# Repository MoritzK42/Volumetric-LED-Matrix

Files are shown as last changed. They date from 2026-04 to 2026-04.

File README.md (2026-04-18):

# Volumetric LED Matrix
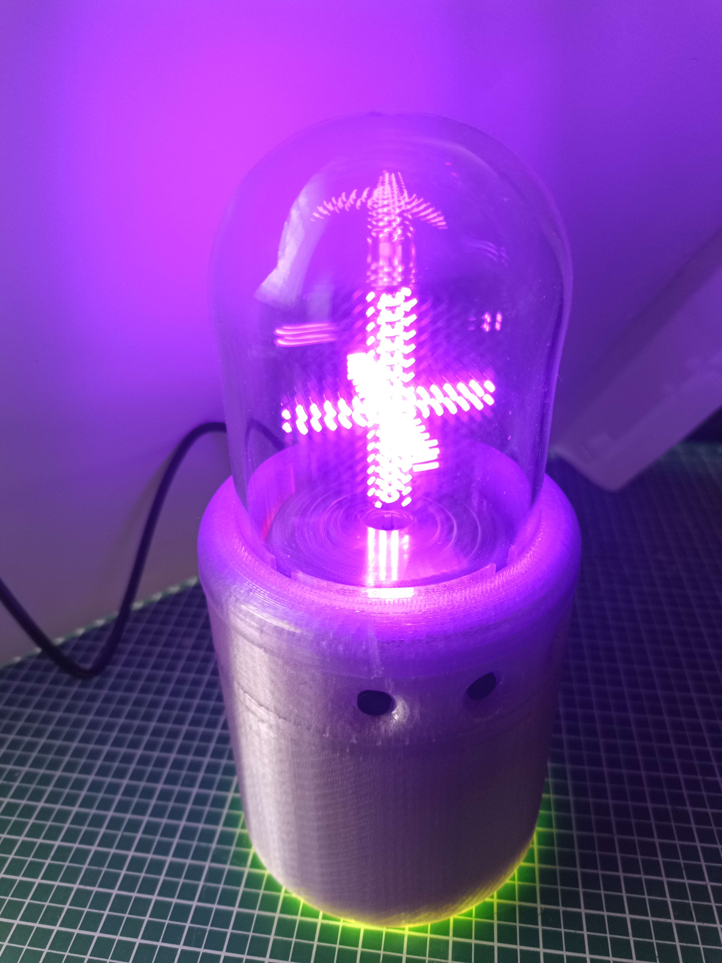
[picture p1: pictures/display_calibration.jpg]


## About the project
This project was inspired by mitxelas tiny volumetric LED display and Nick electronics volumetric lamp project.
It was created in the context of the elective project of the Hochschule für angewandte Wissenschaften (HAW) Hamburg, Germany.
The matrix can display 3D animations on a spinning 16x16 LED matrix, and is powered via USB-C. 

## Hardware
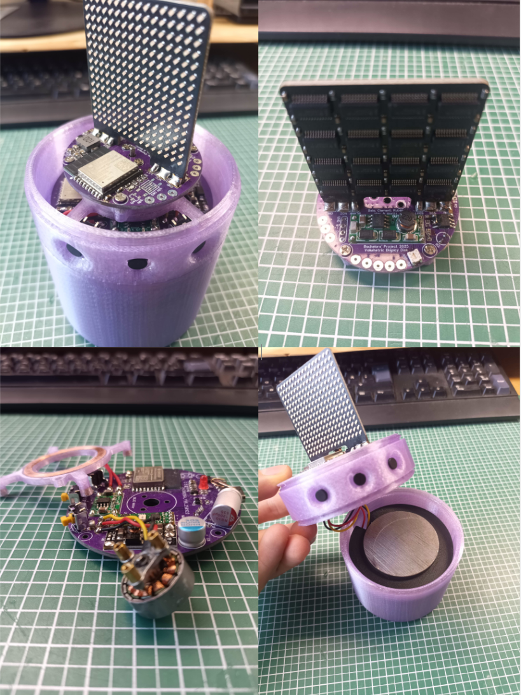
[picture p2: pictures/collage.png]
more pictures can be found in the pictures folder

All used machine screws used are M2 with philips head bought on AliExpress. The used lengths are the following:

For disc to motor: 4 mm

For upper coil holder to PCB: 5 mm

For motor and lower coil holder: 8 mm

The motor stands on 4 mm standoffs, which are spaced with M2 washers to not pierce the motor coils.

All screws must be assembled with loctite for reliable long term use.

The used wireless module is 5V / 1A from AliExpress: https://de.aliexpress.com/item/1005006105734663.html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

The LED RGB ring is 16 LEDs WS2812 RGB module from AliExpress: https://www.aliexpress.com/item/1005006579026411.html?spm=a2g0o.order_list.order_list_main.15.7f645c5fj35ANH

The glass dome was bought on AliExpress

The 12 V mini step up module was bought on AliExpress: https://de.aliexpress.com/item/1005005835656823.html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

The ESC module was bought an AliExpress: https://de.aliexpress.com/item/1005008034100991.html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 (8 A Version)

The BLDC motor was bought on AliExpress: https://de.aliexpress.com/item/1005006110056005.html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

The 16x16 LED Matrix was assembled by JLCPCB PCBA service.

The other circuit boards where assembled by hand.

The wireless coils where glued into the holders (make sure to remove the small piece of tape beforehand) with superglue.
Unfortunately, the matrix suffers from imbalance and thus heavy vibrations when spun. Thus, a 50 mm diameter and 52 mm tall piece of round steel was integrated into to the base as counterweight, aswell as a silicone pad on the bottom to further dampen vibrations. The power to the spinning top part is transported wireless from the base.
The choosen BLDC ESC was rather cheap and especially with a weak power supply, the motor cannot be started up.
The 5 V USB-C power supply must be strong. Not all power supplys work. Anker power banks and supplys have tested good for purpose of powering the volumetric led matrix.
Sometimes the animations or pictures show small glitches. This is a known issue still to be solved.
The filament for the wireless coil spool holders must be capable to withstand higher temperatures without bending itself.
Also, a 1200 uF polymer capacitor was added between USB-C 5 V and GND to further improve stability. Two 22 uf 0805 ceramic capacitors have been added to the base ESP32 input in parallel to the 100 nf and 10 uf decoupling capacitors since there have been issues with the ESP32 crashing when sending wireless commands to the disc ESP32. This issue may have been fixed also by reducing the TX power level in software.

## Software and operation
The Bitmap converter is written in C# and used to convert the Blender generated bitmaps of a frame or animation into a single header file containing a 4-dimensional array. 

The dimensions of the array have the following function:
```c
const uint8_t calibration[8][1][96][32] =
```

1. brightness compensation
2. frame of animation (1 for single 3D Image)
3. subframe (we decided to use 96 subframes per rotation in this project)
4. The single bytes making up the 256 bit LED matrix (8 x 32 = 256)

### Brightness compensation
Since the LEDs closer to the center of the cylindrical axis og the matrix have a lower distance to travel than the outer ones, they would appear to be brighter and thus overexpose the image. To mitigate this, the Bitmap converter automatically compensates the brightness and makes 8 additional frames which are compensated. This is at expense of MCU Flash, because now all frames take up eight times as much flash. But reducing the brightness in run by the MCU has proven to be too slow and would thus hinder a smooth display of the individual frames.

### Led Matrix Base
The LED matrix base containing the motor, buttons, wireless transmitter, 12 V step-up module, the RGB LED ring and position LED is controlled via an ESP32-C3. After plugging in the power, the ESP32 will flash the debugging LED twice and then fade the RGB ring through the colors. After pressing the left button, it will switch on the power to the wireless coil and ESC, which will in turn beep 3 times and turn on if initialized successful. The ESP32 on the disc will be powered and send an acknowledgement if it detects spinning. If not, the ESC initialisation has failed and the base ESP32 will power cycle the ESC to try again. Unfortunately this was the only way the reliably turn on the ESC, since 5 V USB-C supply seemed to be a poor choice and the ESC in general of poor quality. After successful turn on of motor and display, the animations can be cycled trough by pressing the center and right button. A long press will slowly spin the 3D object or animation. When the left button is pressed again, the motor stops and a 2D animation is displayed. The power to ESC and wireless transmitter is cut after 1 min in this state, to mitigate the issue of overheating coils and bent filament if left forgotten in this state.

### Led Matrix Disc
The LED matrix disc containing the LED matrix and LDR with comparator is also controlled via an ESP32-C3. The ESP32 references the start of a rotation via the comparator which compares the voltage from an LDR-resistor divider and potentiometer. Then the time of a rotation is sliced into 96 pieces where the subframes are displayed, altough, the timing is even more precise since there is also the aforementioned brightness compensation and also a settable percentage of on-time 96th time slot the create an effect of single LED dots. Thus, the code is highly optimized to deal with these very strict timing limitations and the hardware SPI-Bus is used to shift out the bits to the display drivers as fast as possible. The LEDs are not multiplexed, since this would, at these already super high refresh rates be almost impossible to deal with. Instead the TI 
The LED matrix disc containing the LED matrix and LDR with comparator is also controlled via an ESP32-C3. The ESP32 references the start of a rotation via the comparator which compares the voltage from an LDR-resistor divider and potentiometer. Then the time of a rotation is sliced into 96 pieces where the subframes are displayed, altough, the timing is even more precise since there is also the aforementioned brightness compensation and also a settable percentage of on-time 96th time slot the create an effect of single LED dots. Thus, the code is highly optimized to deal with these very strict timing limitations and the hardware SPI-Bus is used to shift out the bits to the display drivers as fast as possible. The LEDs are not multiplexed, since this would, at these already super high refresh rates be almost impossible to deal. Instead the 16 bit TI TLC59283DBQR serial shift register LED drivers ICs have been used to drive the LEDs. This choice has proven to be very effective, since the LED Matrix PCBA has performed absolutely flawlessly.

## Rendering animations in Blender
The 3D-Objects can be created in blender. They are then sliced and photographed in 1/96 increments of rotation. To create animations, the process must be repeated with all frames. The naming sceme which can be set in Blender when exporting has to be the following: "nameXX_YY", whereas the XX indicates the number of frame in the animation, and YY indicates the number of subframe in frame. A leading 0 must be added for numbers below 10. A python script in was written in Blender, to automate this process. Powerful hardware must be used to render the frames. They must be exported as singular bitmaps and then they must converted into suitable arrays by the bitmap converter tool. The converted arrays must then be included as header files to the volumetric led matrix disc code.

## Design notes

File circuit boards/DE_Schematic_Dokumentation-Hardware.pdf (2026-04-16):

A | A
B | B
C | C
D | D
E | E
F | F

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
TITLE:
Volumetric Display Assembly Dokumentation | REV: 1.0
Date: | 2025-10-01

Sheet: 1/1
Drawn By: MoritzK

Company: -

## LED Matrix - Reihenfolge Treiber

1 | 2 | 3

4

8

5 | 6 | 7

12

9 | 10 | 11
13 | 14 | 15

Die LED Matrix umfasst eine Gesamtanzahl von 16 x 16 = 256 LEDs.
Die LEDs werden mithilfe von dem LED-Treiber Baustein TLC59283 angesteuert.
Ein LED Treiber kann 16 LEDs ansteuern, weswegen 16 LED Treiber pro Matrix verbaut sind. Um die Leiterbahnenwege m glichst kurz zu halten,
steuern ein Treiber jeweils eine Submatrix von 4 x 4 = 16 LEDs an.

Die Zahlen in der oben stehenden Zeichnung verdeutlichen die Reihenfolge der LED Treiber.

Die LED Treiber werden Seriell ber den SPI-Bus angesteuert.
Ein LED wird mit 16 Bit = 2 Byte Daten gef llt. Sie arbeiten nach dem Shift-Register Prinzip, dass hei t, wenn ein neues Bit an Position 0 gespeichert wird,
r ckt Bit 0 an die Stelle von Bit 1, Bit 1 an die Stelle von Bit 2 usw.
Das letzte Bit, Bit 15 wird dann ber den Serial-Out des vorherigen LED Treibers
zum n chsten LED Treiber Serial-In weitergereicht.
Somit kann die ganze LED Matrix als ein gro er, 256 Bit umfassender Shift-Register betrachtet werden.

## LED Matrix - Submatrix

0 | 1 | 2 | 3
4 | 5 | 6 | 7
11 10 | 9 | 8

15 14 13 12

0

Die entprechende LUT ist als Textdatei in dem Dokumentationsordner enthalten

Die LEDs in der Submatrix mussten leider aus Platz- und Kostengr nden in einer solchen aus Softwaresicht "komischen" Reihenfolge angeordnet werden.

(0,0)

X

Y

(16,16)

(16,0)

(0,16)

So mit m ssen die Koordinaten mithilfe einer Look-Up-Tabelle (LUT)
in die Bit-Position des 256-Bit langen Frames umgewandelt werden.
Die 2D Position (0,0) w rde dann der Bit-Position 12 * 16 + 4 = 196 im 1D Frame entsprechen.
LED Matrix | Disc

# Dokumentation Hardware Volumetric LED Matrix

Der Strom durch die LEDs wird durch einen Widerstand am IREF-Pin der jeweiligen LED-Treiber eingestellt. Der Widerstand wurde auf 15 kOhm festgelegt, was einem Strom pro LED von
(1,208 V / 15 kOhm) * 43,8 = 3,53 mA entspricht.
Der LED Treiber braucht je nach Zustand bis zu max. 11 mA.
Somit betr gt die Maximale Leistungsaufnahme: 3,3 V * 16 * (3,53 mA * 16 + 11 mA) = 3,56 W Die LED Treiber sind nicht dimmbar, jedoch kann bei ausreichend hoher Aktualisierungsrate eine Totzeit implementiert werden, welche einen Dimm-Effekt verursachen kann.
Die Maximale SPI-Frequenz des LED Treibers betr gt 35 MHz.

IO6 - SDAT Serial Data
IO4 - SCLK Serial Clock
IO7 - LAT

Die Ausg nge der LED Treiber werden entsprechend des Zustandes des
internen Shift-Registers angesteuert.

LAT

(Kurzzeitig nach bertragung des Bit-Frames high setzen, um LEDs zu aktualisieren.)

IO3 - BLANK

BLANK
Alle Ausg nge werden abgeschaltet.

IO0 - PULSE

PULSE
Ein Signal pro Umdrehung

IO1 - LED

LED
On-board LED zu Debuggingzwecken

## Pinbelegung ESP32

## Verwendeter Microcontroller:

ESP32-C3-WROOM-02-N4

Die Aktuelle Umdrehungsfrequenz wird mit einem LDR (Light Dependent Resistor) gemessen. Dazu befindet sich auf der Base eine durchgehend leuchtende LED, welche auf die Disc scheint.

LED

LDR

Disc

Base
Der LDR erzeugt ber einen Spannungsteiler
eine Sinusf rmiges Signal, welches mithilfe eines Komparators in rechteckf rmiges Signal umgewandelt wird.

verarbeitet werden.

Somit kann es einfach digital vom ESP32

Die Triggerschwelle kann im ersten Prototyp durch Pot R6
eingestellt werden.
Nach erfolgreicher Einstellung kann in den n chsten Modellen ein fester Widerstand verbaut werden.

## Umdrehungssignal

## VCC Supervisor

Falls Probleme durch instabile Stromversorgung auftreten, kann optional
ein VCC Supervisor IC verbaut werden, welcher den ESP32 bei einer Spannung von kleiner 2,93 V zur cksetzt.

# Base

## Pinbelegung ESP32

IO6 - BTN1
IO7 - BTN2
IO2 - BTN3
IO5 - LED_ESC
IO4 - WS2812
IO0 - LED_THT
IO1 - LED
IO3 - ESC
IO10 - EN_PWR

BTNx
Buttons au erhalb des Geh uses

LED_THT
Through-Hole LED (f r Pulse Signal) EN_PWR
Stromversorgung f r ESC, DC-DC Wandler & Wireless Power Module

LED_THT und EN_PWR sollten vor Start des ESC aktiviert sein.
Die durch EN_PWR angesteuerten Mosfets k nnen ber R15 gebr ckt werden. Es kann optional ein I2C Display verwendet werden.
C8 kann optional verbaut werden, falls extra Gl ttung ben tigt wird.

LED
On-board LED zu Debuggingzwecken

von kleiner 2,93 V zur cksetzt.

ein VCC Supervisor IC verbaut werden, welcher den ESP32 bei einer Spannung

Falls Probleme durch instabile Stromversorgung auftreten, kann optional

## VCC Supervisor

Active Low!

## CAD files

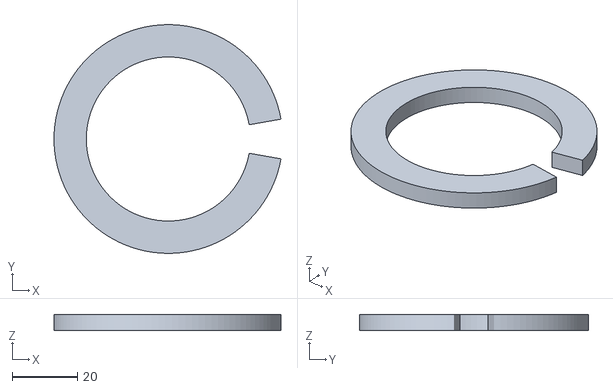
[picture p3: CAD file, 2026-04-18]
3D Print Files STL/V4/Steel Weight Constraint.stl
69.5 x 70.0 x 5.00

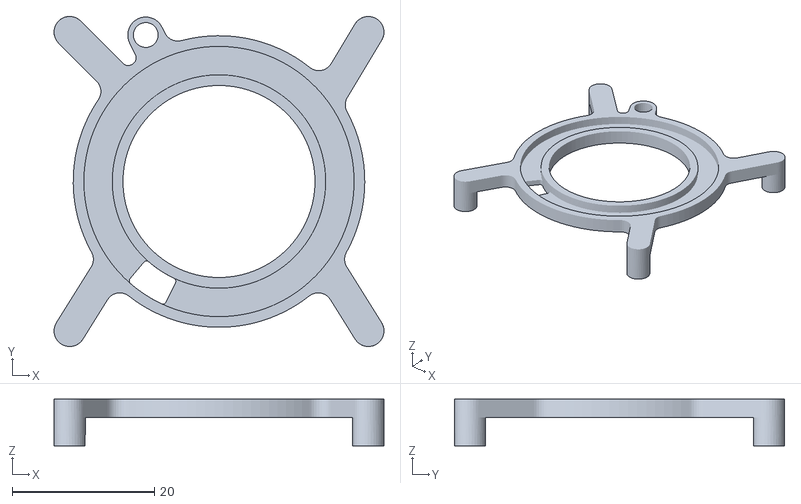
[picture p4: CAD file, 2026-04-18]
3D Print Files STL/V4/Transmitter Coil Case Big Hole.stl
46.4 x 46.4 x 6.60

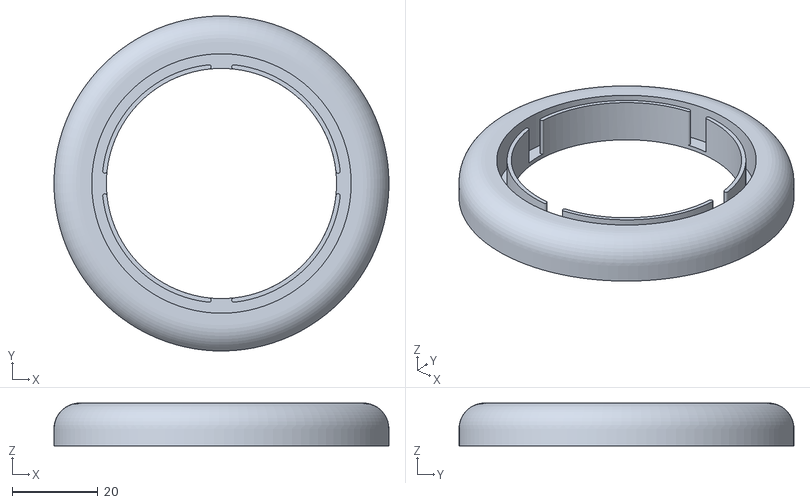
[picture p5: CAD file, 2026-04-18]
3D Print Files STL/V4/Top Housing no markers Lock Interference fixed.stl
78.0 x 78.0 x 10.0

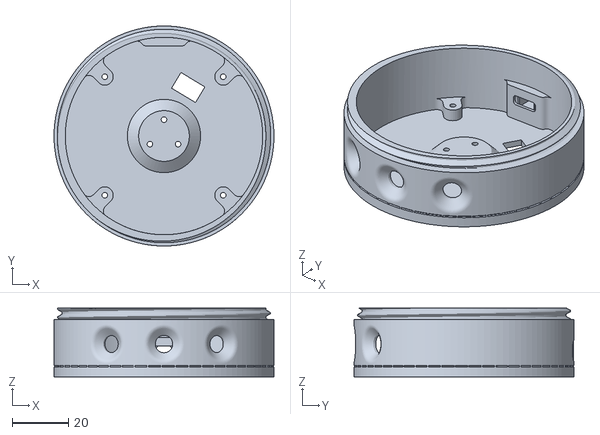
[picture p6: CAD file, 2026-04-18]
3D Print Files STL/V4/Center Housing with Custom Supports.stl
78.0 x 78.0 x 24.3

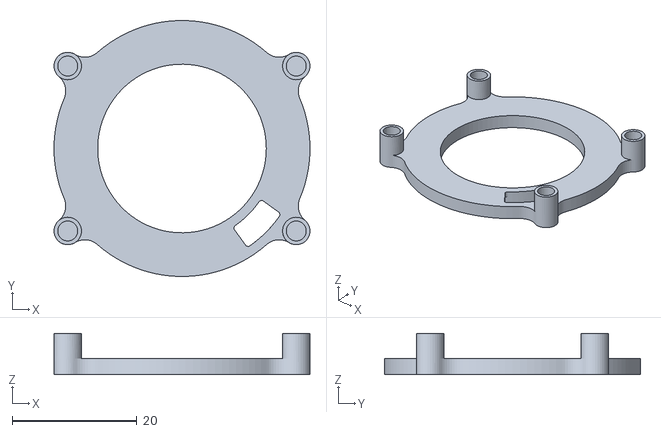
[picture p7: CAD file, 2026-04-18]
3D Print Files STL/V4/Receiver Coil Case Big Hole.stl
41.0 x 41.0 x 6.60

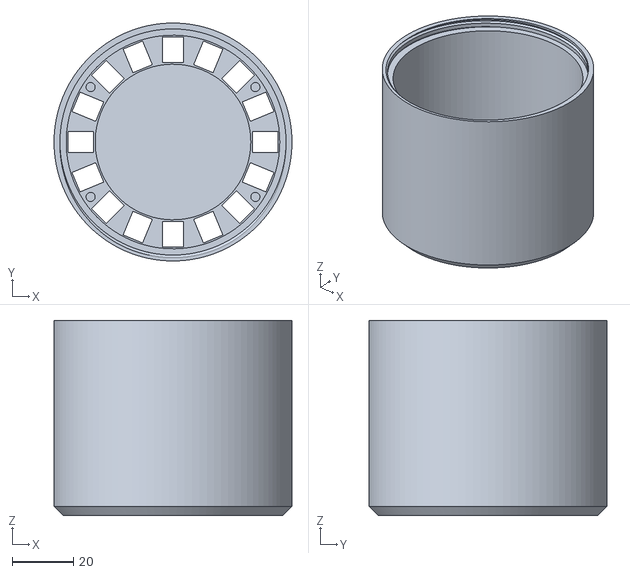
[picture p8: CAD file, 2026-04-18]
3D Print Files STL/V4/Bottom Housing.stl
78.0 x 78.0 x 64.0

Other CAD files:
Blender Files/Animation.blend
Blender Files/CubeAnimation.blend
Blender Files/WindTurbine.blend

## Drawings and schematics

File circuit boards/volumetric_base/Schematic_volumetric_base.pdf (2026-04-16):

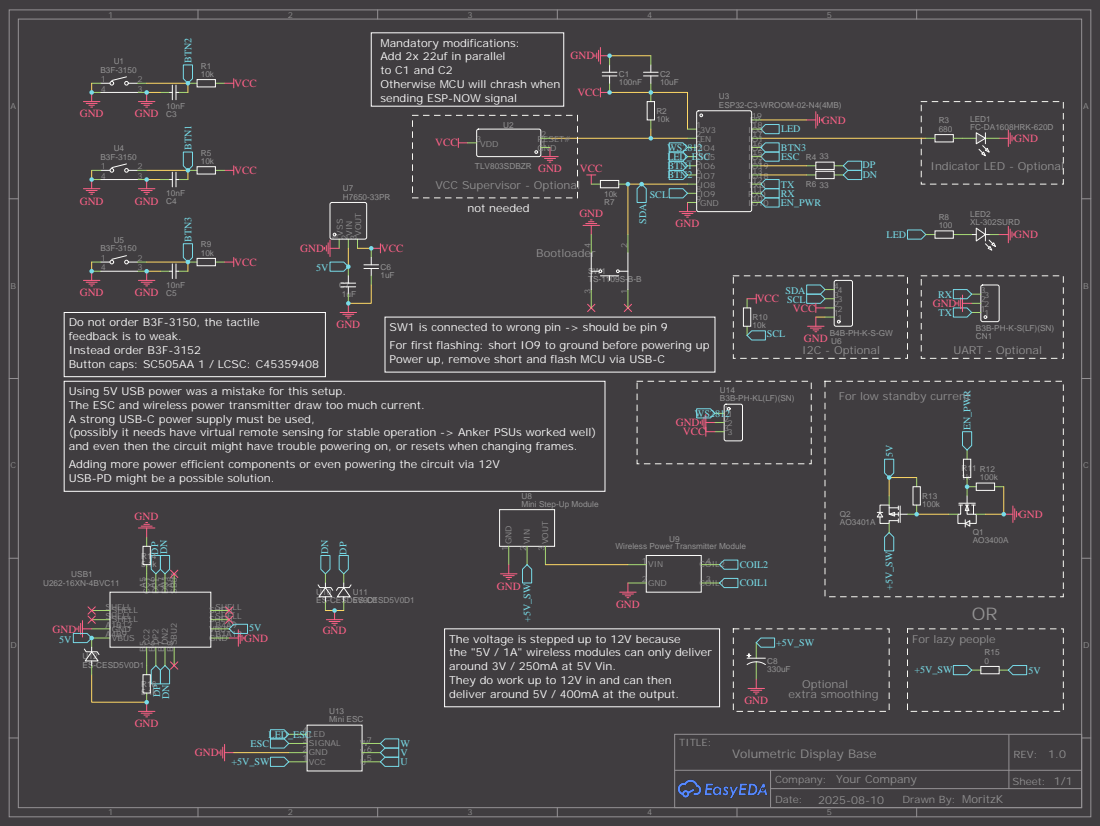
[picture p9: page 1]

Mandatory modifications:
Add 2x 22uf in parallel
to C1 and C2
Otherwise MCU will chrash when
sending ESP-NOW signal

Do not order B3F-3150, the tactile
feedback is to weak.
Instead order B3F-3152

SW1 is connected to wrong pin -> should be pin 9
For first flashing: short IO9 to ground before powering up

Using 5V USB power was a mistake for this setup.
The ESC and wireless power transmitter draw too much current.
A strong USB-C power supply must be used,
(possibly it needs have virtual remote sensing for stable operation -> Anker PSUs worked well)
and even then the circuit might have trouble powering on, or resets when changing frames.
Adding more power efficient components or even powering the circuit via 12V
USB-PD might be a possible solution.

For low standby current

Mini Step-Up Module

Wireless Power Transmitter Module
VIN 1

The voltage is stepped up to 12V because
the "5V / 1A" wireless modules can only deliver
around 3V / 250mA at 5V Vin.
They do work up to 12V in and can then
deliver around 5V / 400mA at the output.

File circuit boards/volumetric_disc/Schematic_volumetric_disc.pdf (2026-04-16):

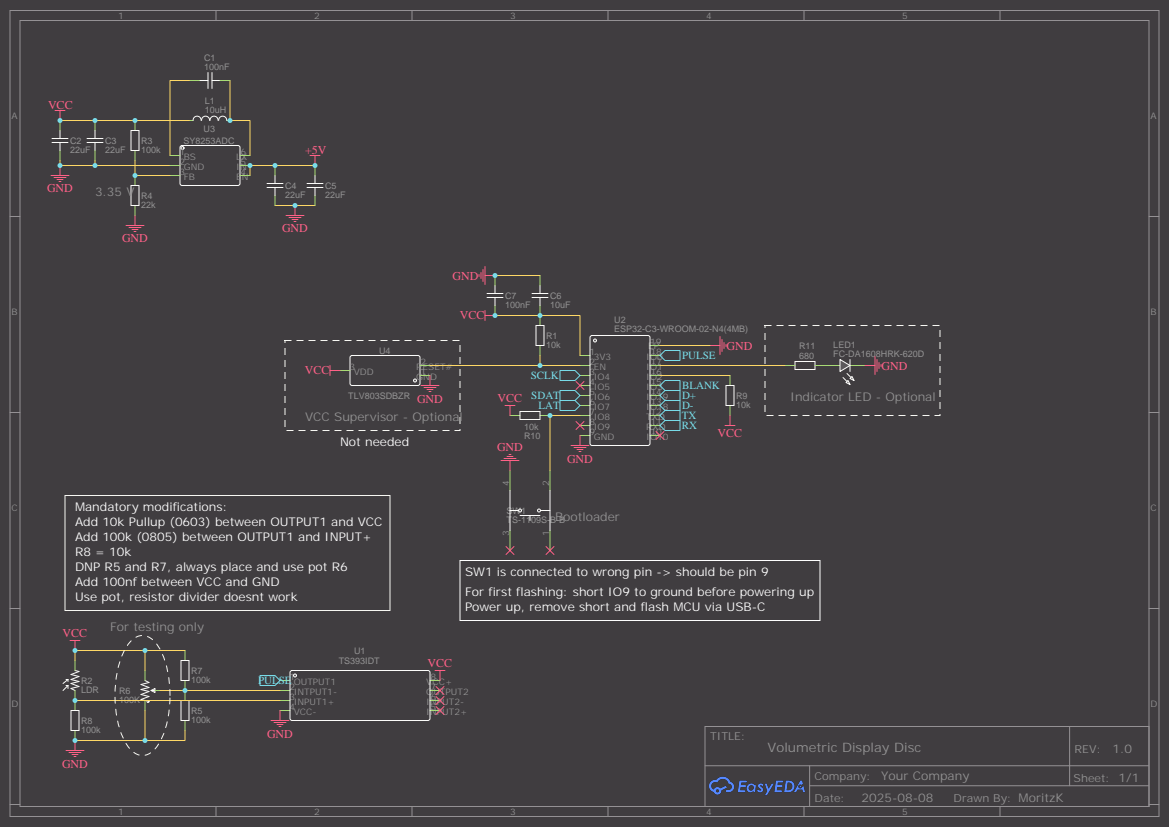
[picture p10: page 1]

Mandatory modifications:
Add 10k Pullup (0603) between OUTPUT1 and VCC
Add 100k (0805) between OUTPUT1 and INPUT+
Add 100nf between VCC and GND
Use pot, resistor divider doesnt work

For first flashing: short IO9 to ground before powering up
Power up, remove short and flash MCU via USB-C

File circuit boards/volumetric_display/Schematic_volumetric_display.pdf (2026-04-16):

A | A

1

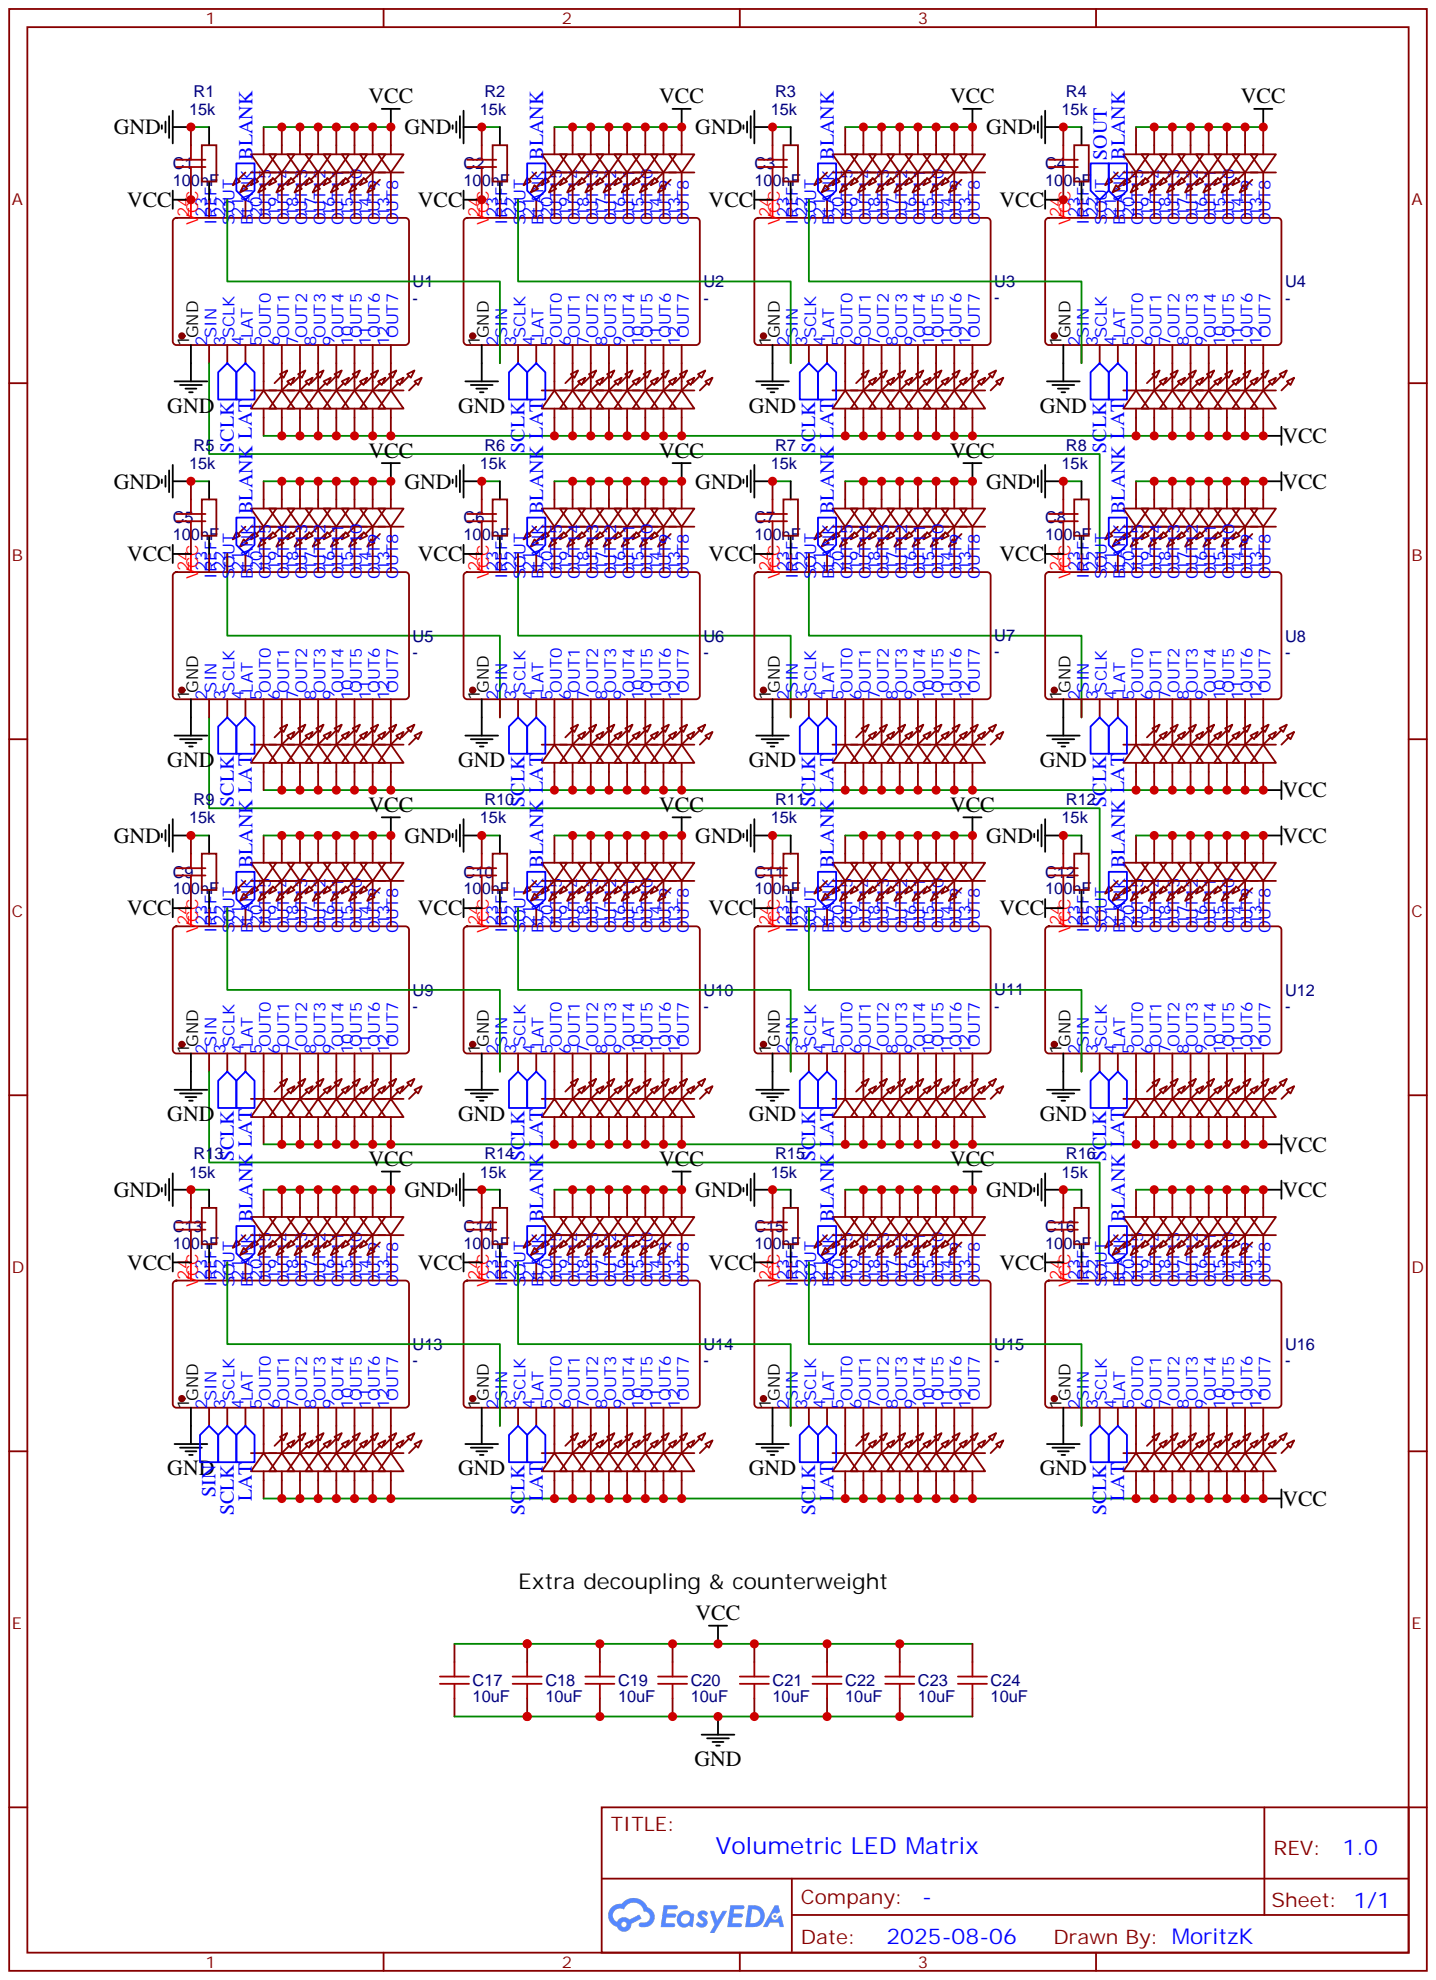
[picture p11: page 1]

OUT7 12 OUT8 13 OUT9 14 OUT10 15 OUT11 16 OUT12 17 OUT13 18 OUT14 19 OUT15 20 BLANK 21 SOUT 22 IREF 23 VCC 24

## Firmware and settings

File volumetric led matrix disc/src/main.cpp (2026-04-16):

/*
Bachelorprojekt 2025
volumetric led matrix disc

Copyright (c) 2026 Moritz Koslowski

Permission is granted to use, copy, and modify this source code
for private, non-commercial purposes only.

Any commercial use, distribution, sublicensing, or inclusion
in a commercial product or service is strictly prohibited
without prior written permission from the copyright holder.

THE SOFTWARE IS PROVIDED "AS IS", WITHOUT WARRANTY OF ANY KIND.
*/

#include <Arduino.h>
#include <SPI.h>
#include <esp_now.h>
#include <esp_wifi.h>
#include <WiFi.h>
#include "font5x7.h"
#include "loading2D.h"

#include "windrad_1.h"
#include "drehrad_8.h"
#include "SE_1.h"
#include "widesky_1.h"
#include "nightsky_1.h"
#include "rollingframe_18.h"
#include "rooollingframe_24.h"
#include "SEseperate_1.h"
#include "bird_7.h"
#include "fireanimation_9.h"

#include "calibrationCo.h"
#include "pokal.h"
#include "wireframecube.h"
#include "campfiremedium_8.h"

#define ROT_OFFSET_SLOWNESS 2       //slowness of object rotation -> 1 = max speed, 1/96th increment each revolution
#define ROT_RESULOTION 95           //subframe amount -1
#define ON_TIME_PERCENT 1           //percentage of time per subframe time slot an LED is switched on (1 = 1%)
#define DISPLAY_2D_DELAY 100        //delay between 2D frames in milliseconds
#define LOADING_ANIMATION_FRAMES 9  //amount of frames in the loading animation
#define MAX_TX_POWER 20             // units of 0.25 dBm, so = 5 dBm | max: 80 = 20 dBm - high TX power leads to MCU chrashing sometimes

#define AMOUNT_3D_IMAGES 6
const uint8_t (*frameptr[AMOUNT_3D_IMAGES])[8][1][ROT_RESULOTION + 1][32] = {&calibrationCo, &wireframecube, &pokal, &windrad_1, &widesky_1, &SEseperate_1};

#define AMOUNT_3D_ANIMATIONS 4
struct sAnimation
{
  const void *ptr;
  const int frameAmount;
  const int animationSlowness;

}typedef sAnimation;

//array struct of: {pointer to animation array, number of frames, animation slowness}
sAnimation animations[AMOUNT_3D_ANIMATIONS] = 
{
  {drehrad_8, 8, 1}, 
  {rooollingframe_24, 24, 2},
  {bird_7, 7, 2},
  {campfiremedium_8, 8, 2}
};


#define SDAT 6
#define SCLK 4
#define LAT 7
#define BLANK 3
#define PULSE 0
#define LED 1


uint8_t baseAddress[] = {0xf7, 0xd9, 0xf9, 0x86, 0xcf, 0x11};
uint8_t discAddress[] = {0x6e, 0x10, 0x32, 0x8d, 0xe8, 0xff};
esp_now_peer_info_t peerInfo;

uint64_t onUs = 0;
volatile unsigned long long lastTimeUs = 0;
volatile unsigned long long deltaT = 0;
volatile unsigned long long currentTimeUs = 0;
volatile bool pulseFlag = false;

byte timeSlots = ROT_RESULOTION;

int currentFrame = 0;
int frameCounter = 0;
int luxCompCounter = 0;
uint8_t nothing[32] = {};

//####### display3DMatrixV2 #########
uint64_t deltaT_64 = 0;
uint64_t resolution_64 = 0;
uint64_t slotTime = 0;
uint64_t onTime = 0;
//###################################

int animationFrameCounter = 0;
int animationFrameCounterDivider = 0;
bool animationFrameCounterDividerHelper = false;

bool rotateCW = false;
bool rotateCCW = false;
int rotOffsetCounter = 0;
int offsettedTimeSlots = 0;
int rotationOffsetCounterDivider = 0;
bool rotationOffsetCounterDividerHelper = false;

bool spinning = false;
volatile unsigned long rotations = 0;

int currentLoadingFrame = 0;
unsigned long loadingMillis = 0;

uint8_t Letter[32]  = {};

bool timeSlotWasZero = false;
int rotOffset = 0;
int rotOffsetHelper = 0;

int subsubStep = 0;
bool intTRIG = false;

void ISR_PULSE();
void displayFrameSPI8(uint8_t frame8Bit[32]);
void getMacAddress();
void setupESPNOWtransmit();
void setupESPNOWreceive();
void changeMACAddress();
void display3DMatrix();
void display2DAnimation();
void print2DLetters();
void actOnINt();
void displayLoading();

void setup() 
{
  pinMode(LED, OUTPUT);
  pinMode(PULSE, INPUT_PULLUP); //active LOW
  attachInterrupt(digitalPinToInterrupt(PULSE), ISR_PULSE, RISING);
  
  pinMode(SDAT, OUTPUT);
  pinMode(SCLK, OUTPUT);
  pinMode(LAT, OUTPUT);
  pinMode(BLANK, OUTPUT);

  changeMACAddress();
  setupESPNOWtransmit();
  SPI.begin();

  displayFrameSPI8(nothing);
 
  //confirm successful setup by blinking onboard LED
  digitalWrite(LED, HIGH);
  delay(200);
  digitalWrite(LED, LOW);
  delay(200);
}

void loop() 
{
  if(rotations > 2)
  {
    if(!spinning)
    {
      spinning = true;
      for(int i = 0; i < 5; i++)
      {
        uint8_t message = 1;
        esp_now_send(baseAddress, (uint8_t *) &message, sizeof(message));
        delay(2);
      }
      
      setupESPNOWreceive();
    }
    if(deltaT > 1E5) //disc not spinning, or spinning very slowly
    {
      displayLoading();
      //display2DAnimation();
    }
    else
    {
      display3DMatrix();
    }
  }
  else
  {
    spinning = false;
    uint8_t message = 0;
    esp_now_send(baseAddress, (uint8_t *) &message, sizeof(message));
    //display2DAnimation();
    displayLoading();
  }
}

//cycle time optimized function, can now deal with gradual brightness reduction
void display3DMatrix()
{
  const uint64_t now = (uint64_t)esp_timer_get_time();
  if(pulseFlag)
  {
    pulseFlag = false;
    timeSlots = ROT_RESULOTION; //reset timeSlots
    //calculate new slot-parameter (without using floats)
    deltaT_64 = deltaT;
    resolution_64 = ROT_RESULOTION;
    slotTime = (deltaT_64 / (resolution_64 ? resolution_64 : 1)); //failsafe, prevent division by zero
    onTime = (uint32_t)((slotTime * (uint64_t)ON_TIME_PERCENT) / 100ULL);
  }

  if(now - currentTimeUs >= slotTime * (ROT_RESULOTION - timeSlots))
  {
    if(timeSlots > 0)
    {
      timeSlots--;
      animationFrameCounterDividerHelper = true;
      rotationOffsetCounterDividerHelper = true;
    }

    //used to rotate the 3D Image/Animation in increments of 1 / ROT_RESULOTION 
    if(rotateCW)
    {
      offsettedTimeSlots = timeSlots + rotOffsetCounter;
      if(offsettedTimeSlots > ROT_RESULOTION)
      {
        offsettedTimeSlots -= (ROT_RESULOTION + 1);
      }
    }
    else if(rotateCCW)
    {
      offsettedTimeSlots = timeSlots - rotOffsetCounter;
      if(offsettedTimeSlots < 0)
      {
        offsettedTimeSlots += (ROT_RESULOTION + 1);
      }
    }
    else
    {
      offsettedTimeSlots = timeSlots;
      rotOffsetCounter = 0; //always set to zero to start the rotation without jumping around
    }

    onUs = (uint64_t)esp_timer_get_time();
  }

  if(now - onUs > slotTime * onTime)
  {
    displayFrameSPI8(nothing);
  }
  else
  {
    //change luxCompCounter to shift through the 8 brightness compensated frames
    if(++luxCompCounter >= 8) luxCompCounter = 0;
    
    uint8_t dma32[32];
    const uint8_t* src;
    
    if(currentFrame < AMOUNT_3D_IMAGES)
    {
      src = (*frameptr[currentFrame])[luxCompCounter][0][offsettedTimeSlots];
    }
    else
    {
      int idx = currentFrame - AMOUNT_3D_IMAGES;
      int frames = animations[idx].frameAmount;
      const uint8_t (*anim)[8][frames][ROT_RESULOTION+1][32] = (const uint8_t (*)[8][frames][ROT_RESULOTION+1][32]) animations[idx].ptr;
      src = anim[0][luxCompCounter][animationFrameCounter][offsettedTimeSlots];

    }
    //copy frame from flash to RAM for jitter free access and smooth SPI shifting
    memcpy(dma32, src, 32);
    displayFrameSPI8(dma32);
  }

  //count up animationFrameCounter to change the frames for animation
  //special logic to slow down frame changing depended on animations->animationSlowness
  if(animationFrameCounterDivider >= animations->animationSlowness)
  {
    animationFrameCounterDivider = 0;
    {
      if(animationFrameCounter < animations[currentFrame - AMOUNT_3D_IMAGES].frameAmount - 1)
      {
        animationFrameCounter++;
      }
      else
      {
        animationFrameCounter = 0;
      }
    }
  }
  
  if(timeSlots == 0 && animationFrameCounterDividerHelper)
  {
    animationFrameCounterDividerHelper = false;
    animationFrameCounterDivider++;
  }

  //count up rotOffsetCounter to be able to rotate the 3D Image
  if(rotationOffsetCounterDivider >= ROT_OFFSET_SLOWNESS)
  {
    rotationOffsetCounterDivider = 0;
    if(++rotOffsetCounter >= ROT_RESULOTION + 1) rotOffsetCounter = 0;
  }

  if(timeSlots == 0 && rotationOffsetCounterDividerHelper)
  {
    rotationOffsetCounterDividerHelper = false;
    rotationOffsetCounterDivider++;
  }
}



void displayLoading()
{

  if(millis() - loadingMillis > DISPLAY_2D_DELAY)
  {
    loadingMillis = millis();
    if(currentLoadingFrame < LOADING_ANIMATION_FRAMES - 1)
    {
      currentLoadingFrame++;
    }
    else
    {
      currentLoadingFrame = 0;
    }
  }
  displayFrameSPI8(loading2D[0][currentLoadingFrame]);
  delay(0); 
  displayFrameSPI8(nothing);
  delay(10); //bad coding
}

void print2DLetters()
{
  bool buffer[256] = {};
  for(int i = 0; i < 5; i++)
  {
    for(int j = 0; j < 8; j++)
    {
      buffer[8 * i + j] = font5x7[65 + i] & (0x01 << j);
    }
  }
  //convBoolTo8Bit(buffer, Letter);
}

void display2DAnimation()
{
  displayFrameSPI8(Letter);
}


//triggered at every rotation, used to calculate period duration
void IRAM_ATTR ISR_PULSE()
{
  rotations = rotations + 1;
  currentTimeUs = esp_timer_get_time(); //returns the time since program start in microseconds
  gpio_set_level((gpio_num_t)LED, HIGH); //faster than digitalWrite... only for debug
  deltaT = currentTimeUs - lastTimeUs;
  lastTimeUs = currentTimeUs;
  //timeSlots = ROT_RESULOTION; //reset timeSlots
  pulseFlag = true;
  gpio_set_level((gpio_num_t)LED, LOW);
}

void actOnINt()
{
  intTRIG = false;
}


void displayFrameSPI8(uint8_t frame8Bit[32])//bool inputFrame[256])
{
  SPI.beginTransaction(SPISettings(25E6, MSBFIRST, SPI_MODE3)); //SPI_MODE0 or SPI_MODE3 work | 35E6 = 35 MHz SPI freq, max of LED driver

  gpio_set_level((gpio_num_t)LAT, LOW); //faster than digitalWrite...
  SPI.writeBytes(frame8Bit, 32); 
  gpio_set_level((gpio_num_t)LAT, HIGH);

  SPI.endTransaction();
}


void getMacAddress()
{
  Serial.begin(115200);
    delay(1000); // uncomment if your serial monitor is empty
    WiFi.mode(WIFI_STA); 
    while (!(WiFi.STA.started())) { // comment the while loop for ESP8266
        delay(10);
    }
    delay(1000);
    Serial.print("MAC-Address: ");
    String mac = WiFi.macAddress();
    Serial.println(mac);
    
    Serial.print("Formated: ");
    Serial.print("{");
    int index = 0;
    for(int i=0; i<6; i++){
        Serial.print("0x");
        Serial.print(mac.substring(index, index+2));
        if(i<5){
            Serial.print(", ");
        }
        index += 3;
    }
    Serial.println("}");
}

void messageReceived(const esp_now_recv_info *info, const uint8_t* incomingData, int len)
{
  //decrement trough frames/animations
  if(incomingData[0] == 1)
  {
    if(currentFrame > 0)
    {
      currentFrame--;
    }
    else
    {
      currentFrame = (AMOUNT_3D_IMAGES + AMOUNT_3D_ANIMATIONS) - 1;
    }
  }

  //increment trough frames/animations
  if(incomingData[0] == 2)
  {
    if(currentFrame < ((AMOUNT_3D_IMAGES + AMOUNT_3D_ANIMATIONS) - 1))
    {
      currentFrame++;
    }
    else
    {
      currentFrame = 0;
    }
  }

  //start/stop rotation clockwise
  if(incomingData[0] == 3)
  {
    rotateCW ^= 1;          //turn on/off 3D rotation clockwise
    rotateCCW = false;  //turn off 3D rotation counter clockwise
  }

  //start/stop rotation counter-clockwise
  if(incomingData[0] == 4)
  {
    rotateCCW ^= 1;         //turn on/off 3D rotation counter-clockwise
    rotateCW = false;  //turn off 3D rotation clockwise
  }
}

void setupESPNOWtransmit()
{
  WiFi.mode(WIFI_STA);
  esp_now_init();
  memcpy(peerInfo.peer_addr, baseAddress, 6);
  peerInfo.channel = 0;
  peerInfo.encrypt = false;
  esp_now_add_peer(&peerInfo);
  esp_wifi_set_max_tx_power(MAX_TX_POWER);  //reduce max TX power, because of unstable power supply and problems with MCU resetting otherwise
}

void setupESPNOWreceive()
{
  WiFi.mode(WIFI_STA);
  esp_now_init();
  esp_now_register_recv_cb(messageReceived);
}

void changeMACAddress()
{
  WiFi.mode(WIFI_STA);
    while (!(WiFi.STA.started())) 
    {
      delay(100);
    }

    esp_wifi_set_mac(WIFI_IF_STA, discAddress);
}
